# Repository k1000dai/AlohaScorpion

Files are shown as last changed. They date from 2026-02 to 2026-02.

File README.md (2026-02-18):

# AlohaScorpion

<p align="center">
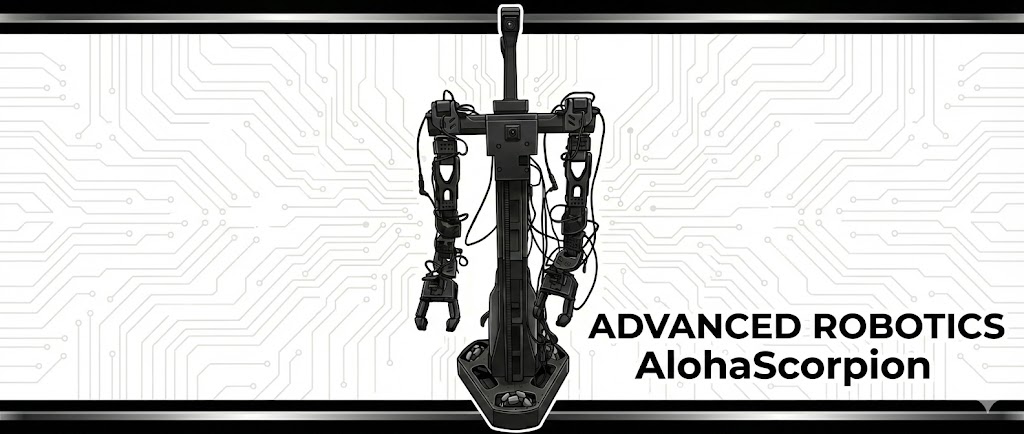
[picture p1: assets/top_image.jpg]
AlohaScorpion_top
  
</p>

AlohaScorpion is a 7 dof + gripper, dual-arm mobile manipulator with lift. It is designed for research and development in robotics, particularly in manipulation and mobile robotics.
This project is heavily inspired by the 

- Lerobot(https://github.com/k1000dai/lerobot)
- Alohamini(https://github.com/liyiteng/AlohaMini)
- Xlerobot(https://github.com/Vector-Wangel/XLeRobot)
- DualScorpion(https://github.com/momoiorg-repository/dual_scorpion)
- PincOpen(https://github.com/pollen-robotics/PincOpen)

## Update Log 
2/14 : Updated to the version 2.0. Better BOM, better chassis design, better arm position, pincopen gripper.

## To Do

- [ ] Add more details to the assembly instructions.
- [ ] Support VLA training.
- [ ] Support URDF and simulators.

## Images
<p align="center">
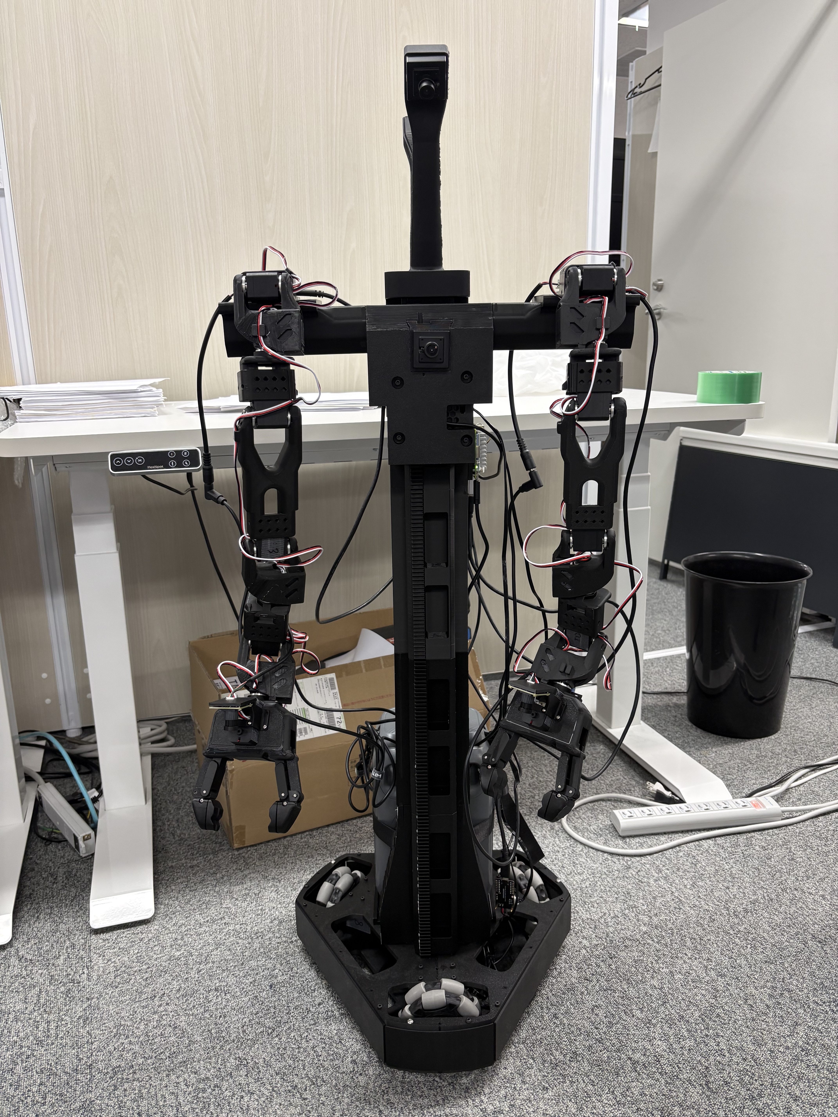
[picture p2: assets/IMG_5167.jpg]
AlohaScorpion
  
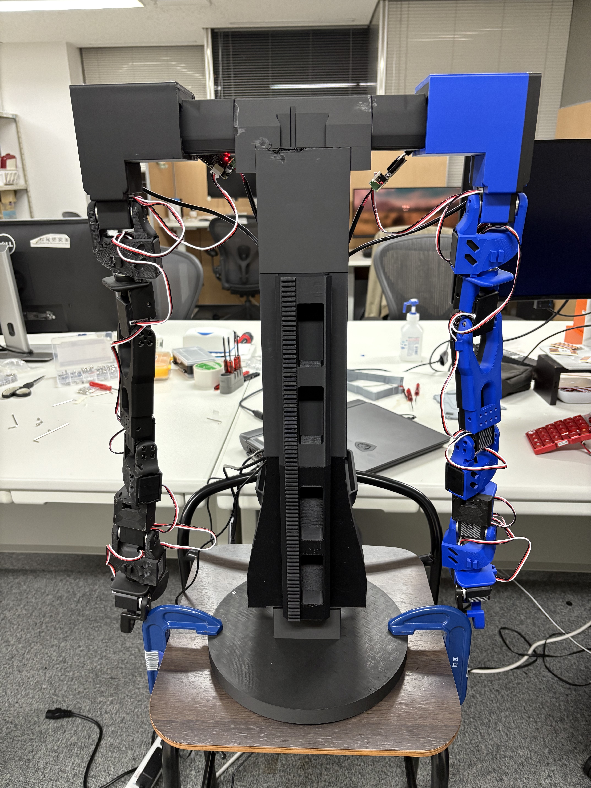
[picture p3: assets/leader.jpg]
leader
  
</p>

## Features
- 7 degrees of freedom per arm for enhanced manipulation capabilities. inspired by dual_scorpion

- Large battery capacity for extended operation time. based on the Xlerobot. Use Anker Solix C300 Portable Power Station 288Wh.

<p align="center">
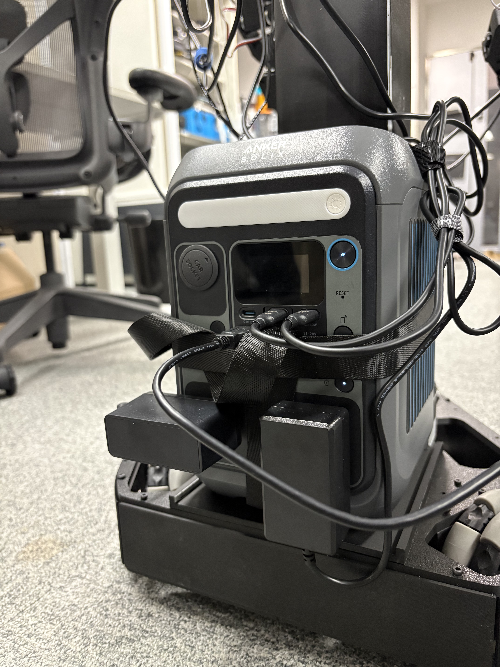
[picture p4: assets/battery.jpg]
battery
  
</p>

- Mobile base for navigation and mobility. based on alohamini. Using the Xlerobot chassis design, stronger and more stable than alohamini's chassis.

<p align="center">
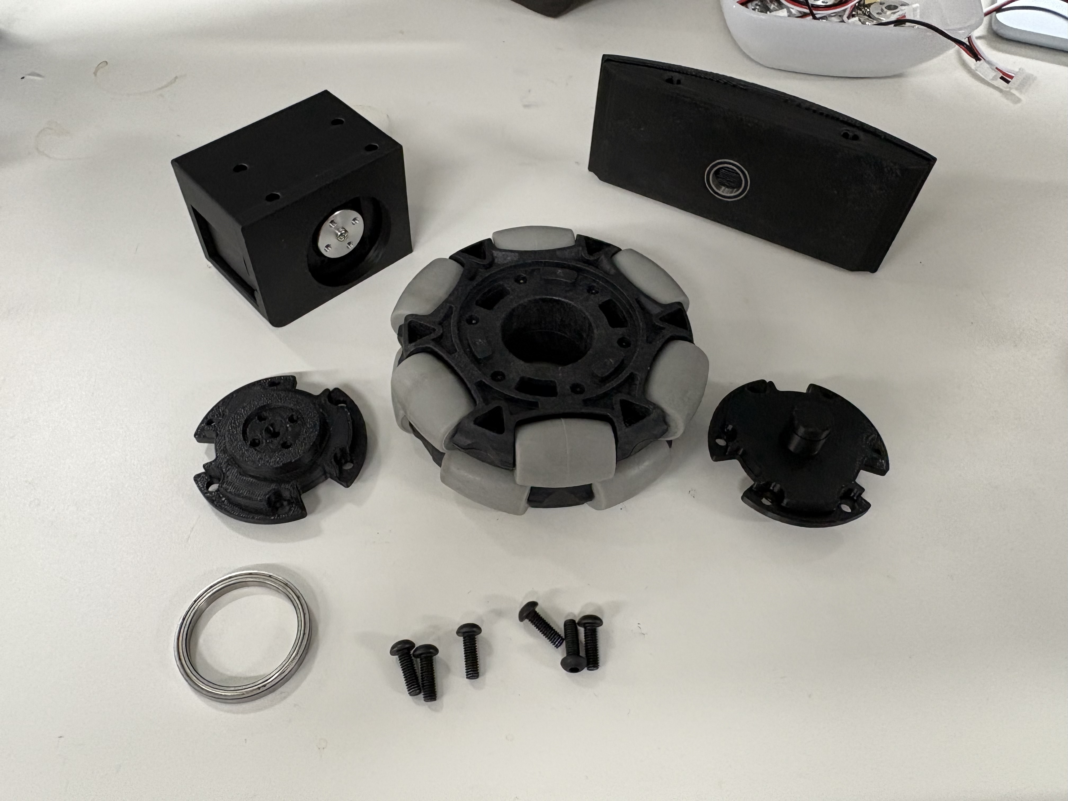
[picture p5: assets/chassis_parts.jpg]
chassis_parts
  
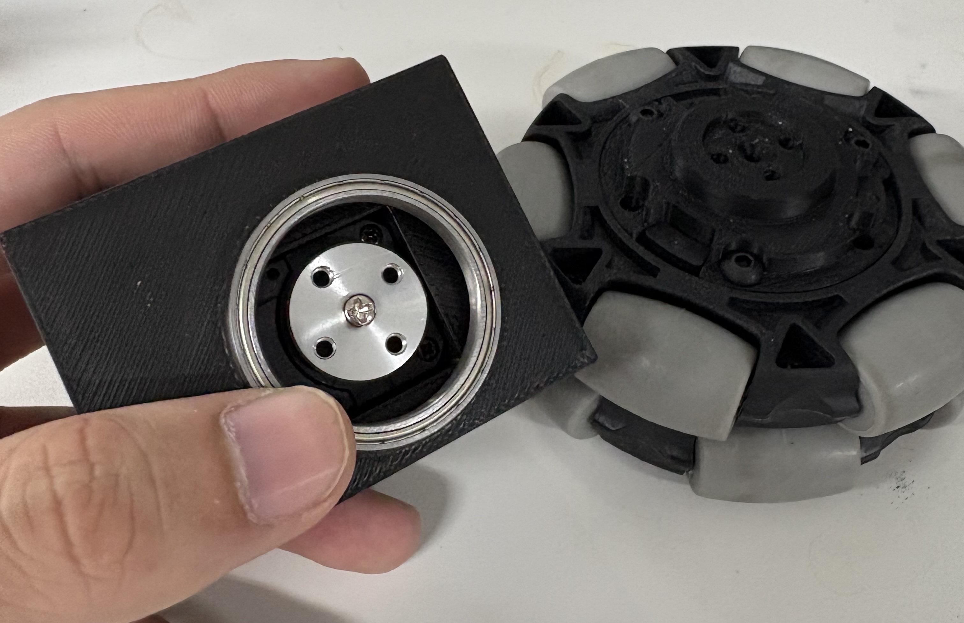
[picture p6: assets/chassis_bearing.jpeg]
chassis_bearing
  
</p>
<p align="center">
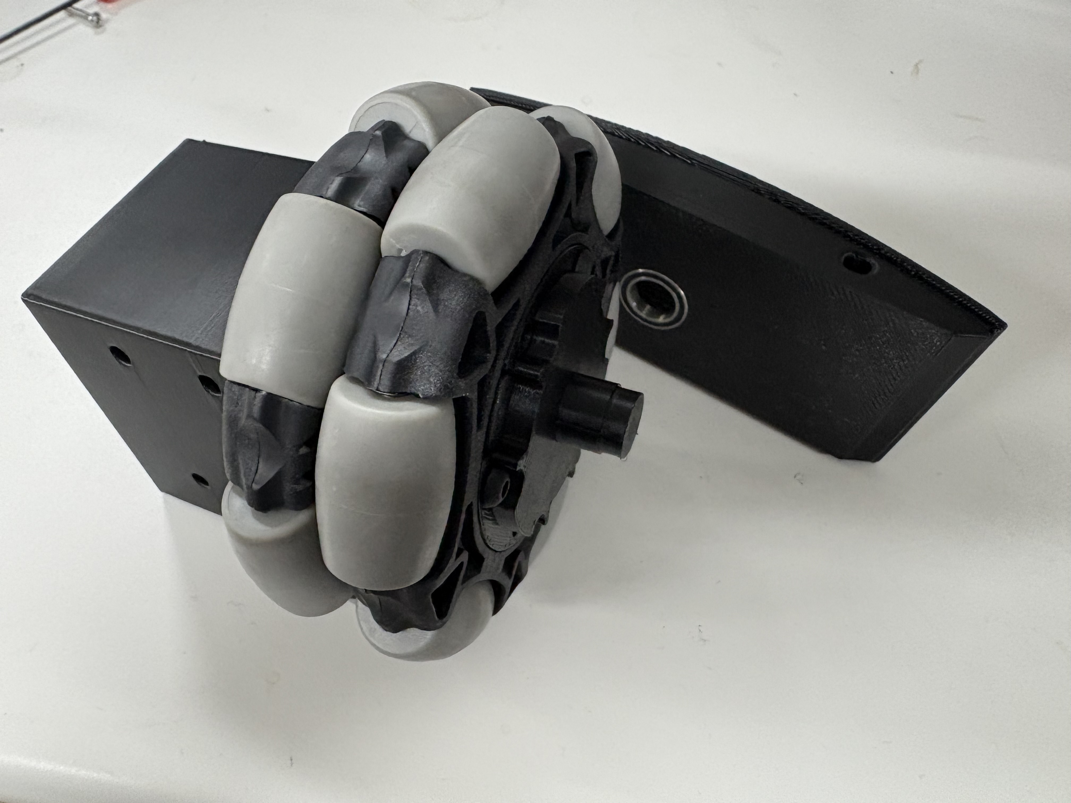
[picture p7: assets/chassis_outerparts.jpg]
chassis_outerparts
  
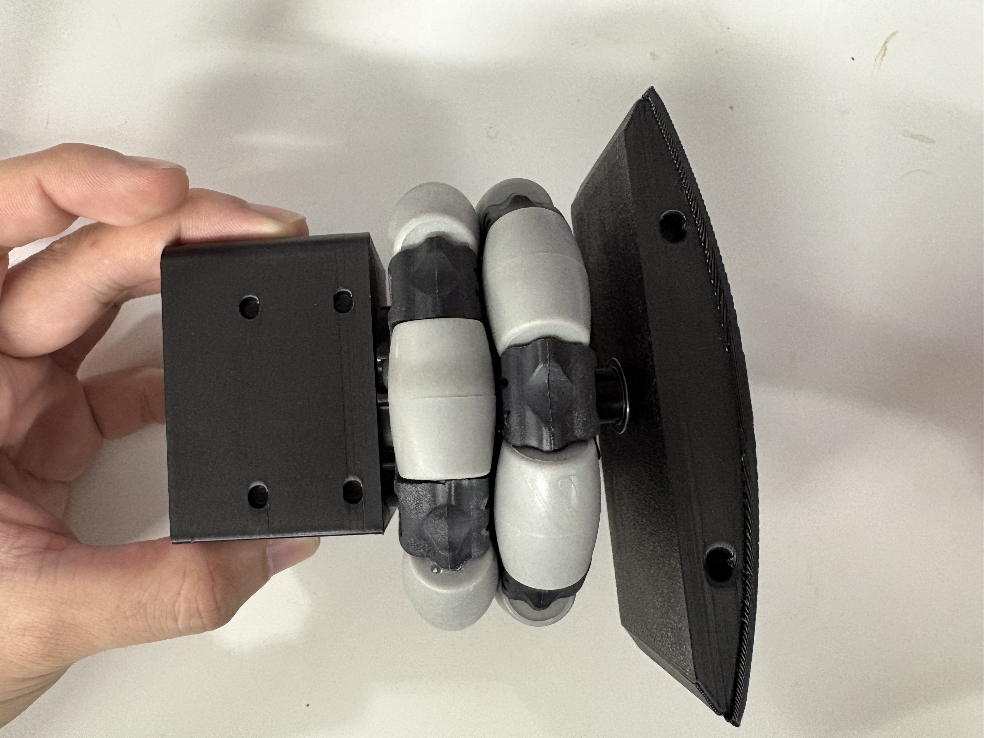
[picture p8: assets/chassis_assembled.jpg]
chassis_assembled
  
</p>

- Gripper for object handling. We use the PincOpen gripper, which is open-source parallel-finger gripper, derived from Pollen Robotics Reachy 2's gripper. It is compatible with the arms of AlohaScorpion.

<p align="center">
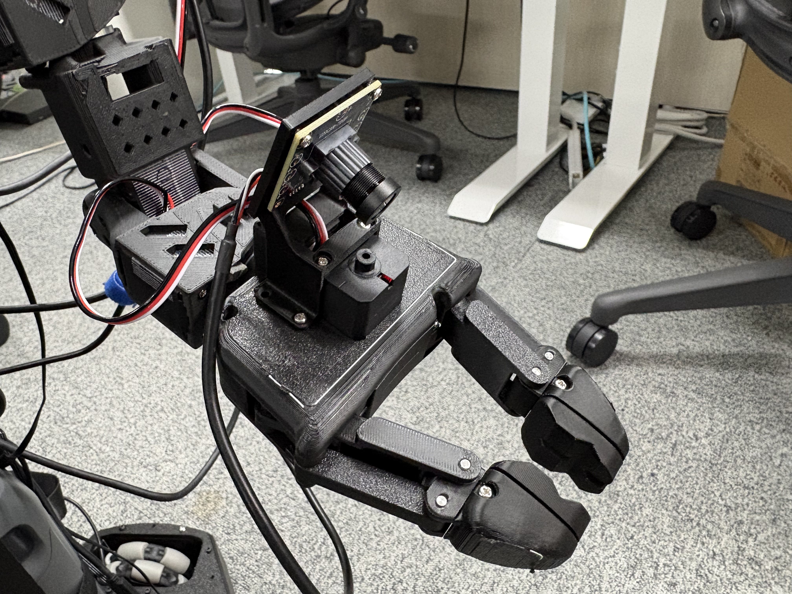
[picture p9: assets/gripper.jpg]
gripper
  
</p>

- Lift mechanism for vertical movement. based on Alohamini.

- Data collection and logging capabilities for research purposes. based on the lerobot framework. compatible with lerobot v0.4.3.

## Bill of Materials (BOM)
The complete Bill of Materials (BOM) can be found in the this Google Sheet : https://docs.google.com/spreadsheets/d/1W7IXB0Fid7SDyZUYEEcC63fRW-HXA5QO-rrAWQz4-Ek/edit?usp=sharing.

If you want to use  parallel-finger gripper, you can refer PincOpen github repository[https://github.com/pollen-robotics/PincOpen] for the BOM and assembly instructions. The gripper is compatible with the arms of AlohaScorpion. You need to use the updated mount plate in hardware/misc/stl/sointerface.stl.

## Assembly Instructions
Please see AlohaMini's assembly instructions as the mobile base and lift mechanism are almost the same.

Also, for the arms, please follow the dual_scorpion's assembly instructions. In order to keep the motor id, we use the 0 ~ 
7 motor for the arms. 8,9,10,11 motors are used for the mobile base and lift mechanism.

## Software

### Environment Setup
We setup the host with raspberry pi 5. You can also use any PC or raspberry pi 5 as the host.

install uv
```
curl -LsSf https://astral.sh/uv/install.sh | sh
```

```
git clone https://github.com/k1000dai/AlohaScorpion.git
cd AlohaScorpion
uv sync  --extra feetech
uv pip install zmq
```

### Running the Software
#### teleoperation
host side
```
python -m lerobot.robots.alohamini_scorpion.lekiwi_host
```

client side
```
python examples/alohamini_scorpion/teleoperate_bi.py \
--remote_ip ip_address_of_host \
```

#### data collection

- sample dataset : https://huggingface.co/datasets/k1000dai/alohascorpion_pick_plate_put_box
host side
```
python -m lerobot.robots.alohamini_scorpion.lekiwi_host
```
client side
```
python examples/alohamini_scorpion/record_bi.py \
--remote_ip ip_address_of_host \
--dataset user/my_dataset_name 
```

#### Replay
host side
```
python -m lerobot.robots.alohamini_scorpion.lekiwi_host
```

client side
```
python examples/alohamini_scorpion/replay_bi.py \
--remote_ip ip_address_of_host \
--dataset user/my_dataset_name
```

#### VLA training

ACT
```
lerobot-train \
  --dataset.repo_id=k1000dai/alohascorpion_pick_plate_put_box \
  --policy.type=act \
  --output_dir=outputs/train/alohascorpion_pick_plate_put_box\
  --job_name=alohascorpion_act \
  --policy.device=cuda \
  --wandb.enable=true \
  --policy.repo_id=k1000dai/alohascorpion_act
```

PI05
```
lerobot-train \↲
    --dataset.repo_id=k1000dai/alohascorpion_pick_plate_put_box \
    --policy.type=pi05 \
    --policy.pretrained_path=lerobot/pi05_base \
    --policy.compile_model=true \
    --policy.gradient_checkpointing=true \
    --output_dir=outputs/train/alohascorpion_pick_plate_put_box\
    --job_name=alohascorpion_pi05 \
    --policy.device=cuda \
    --policy.dtype=bfloat16 \
    --policy.freeze_vision_encoder=false \
    --policy.train_expert_only=false \
    --wandb.enable=true \
    --policy.repo_id=k1000dai/alohascorpion_pi05 \
    --batch_size=32
```

#### Evaluation model
```
python examples/alohamini_scorpion/evaluate_bi.py \
  --num_episodes 1 \
  --fps 10 \
  --episode_time 180  \
  --task_description "task_description"  \
  --hf_model_id k1000dai/act_alohascorpion  \
  --hf_dataset_id k1000dai/evaldataset   \
  --remote_ip ip_address_of_host
```
## License
This project is licensed under the Apache 2.0 License - see the [LICENSE](LICENSE) file for details.

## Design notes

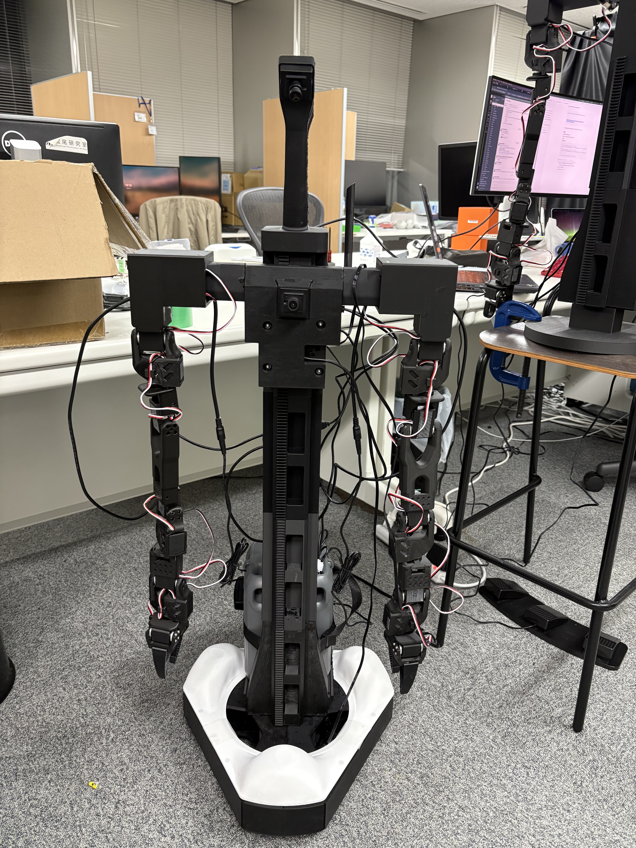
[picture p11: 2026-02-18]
assets/mainimage.jpg

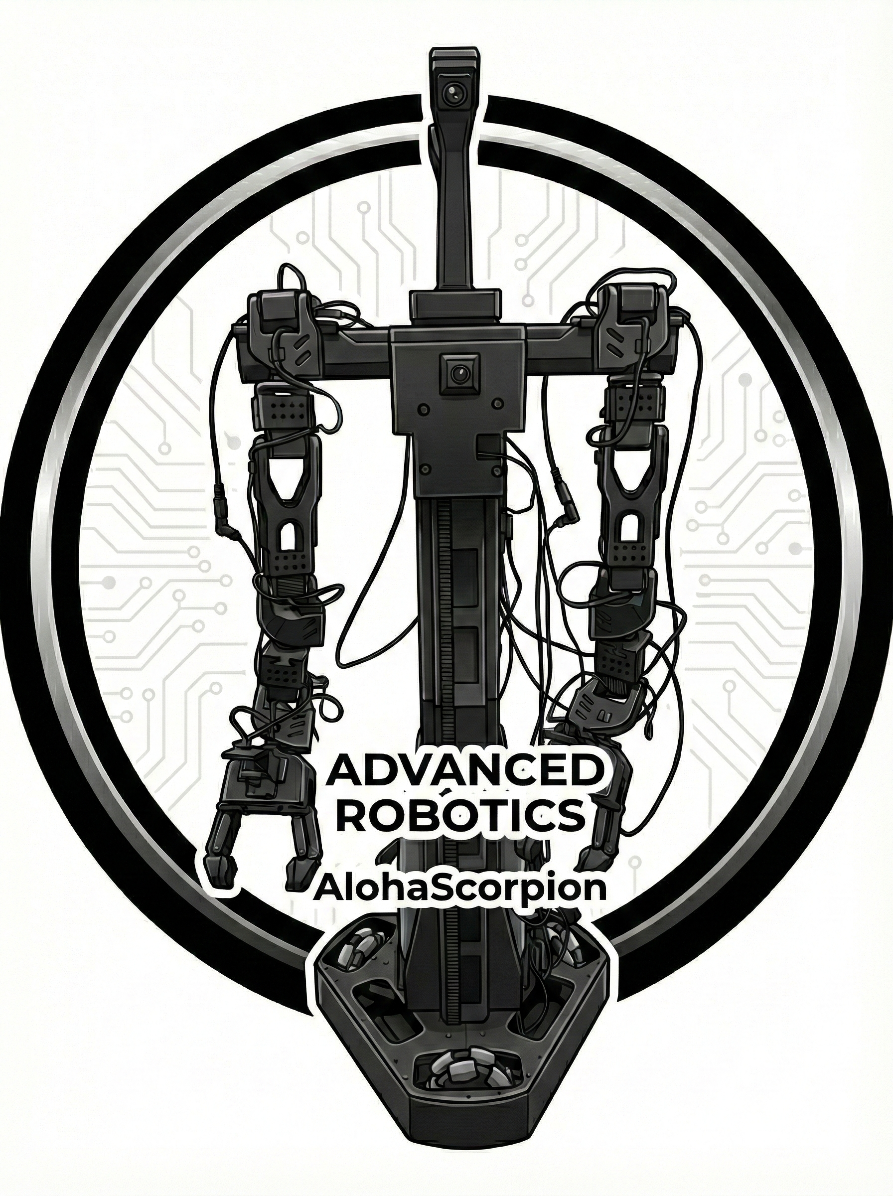
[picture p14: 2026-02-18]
assets/log.png

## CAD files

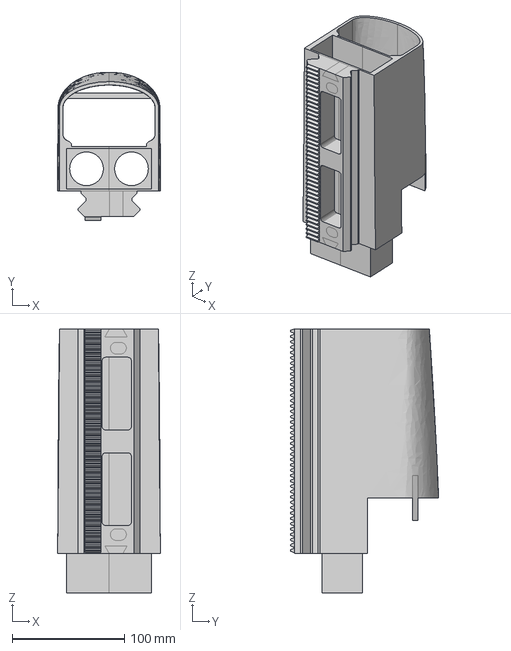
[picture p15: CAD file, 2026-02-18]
hardware/mobilebase/step/O_Main_Assembly_Post3.step
91.5 x 132.0 x 235.0 mm

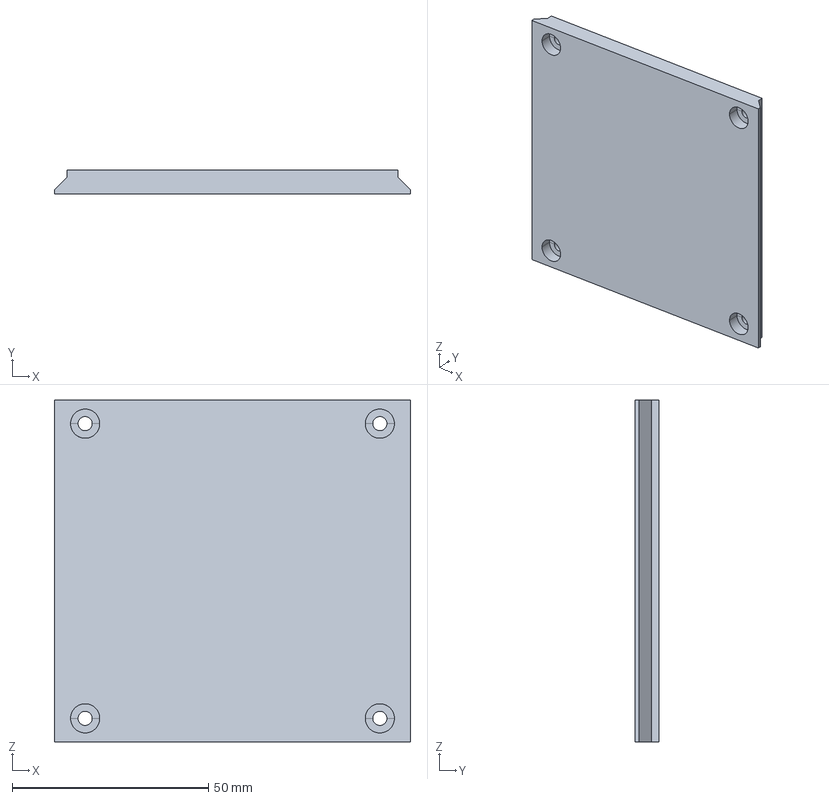
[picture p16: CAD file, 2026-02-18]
hardware/mobilebase/step/OB_Main_Monitor_Connector.stp
90.6 x 6.00 x 87.0 mm

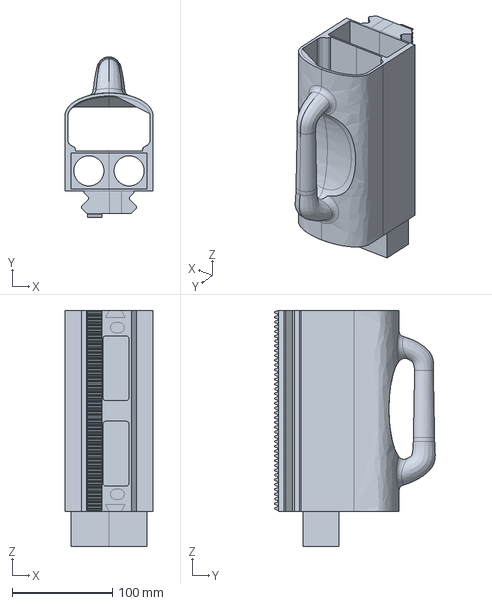
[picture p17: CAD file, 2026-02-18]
hardware/mobilebase/step/O_Main_Assembly_Post2.stp
88.1 x 159.9 x 235.0 mm

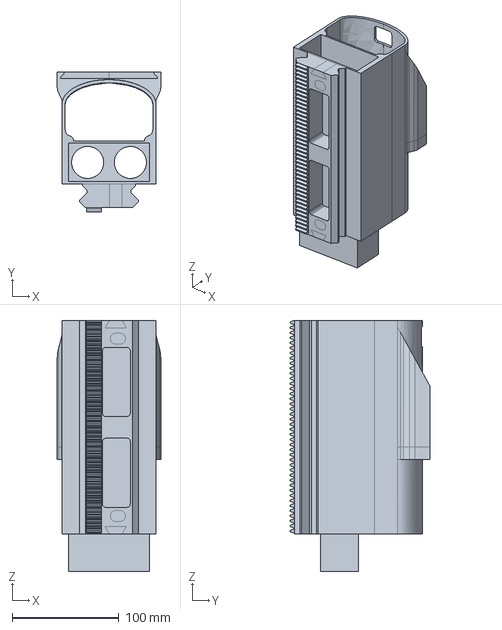
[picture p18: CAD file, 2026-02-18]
hardware/mobilebase/step/O_Main_Assembly_Post1.stp
97.0 x 130.7 x 235.0 mm

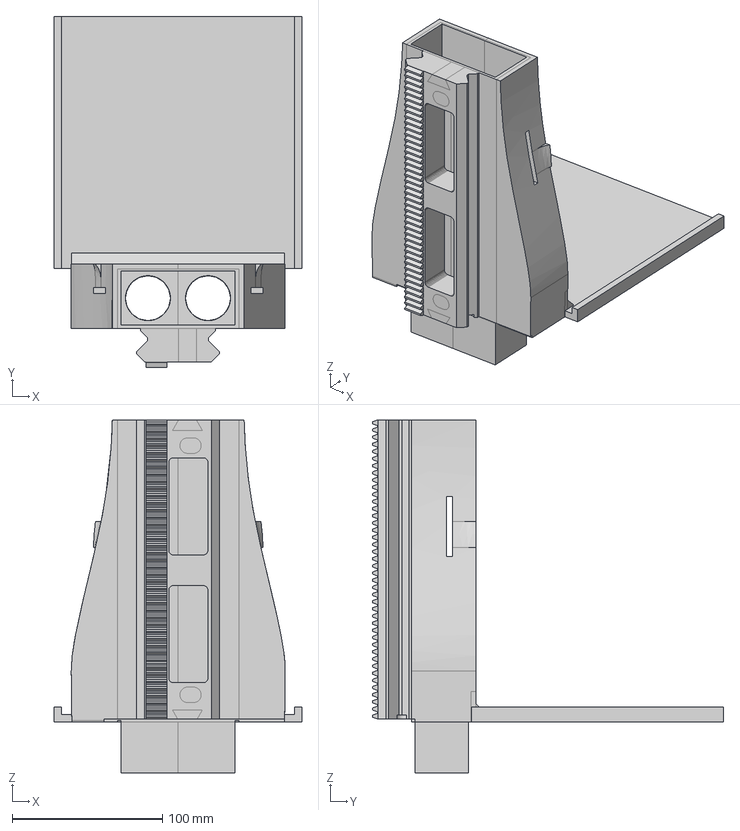
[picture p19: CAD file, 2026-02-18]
hardware/mobilebase/step/O_Main_Assembly_Post4_solaris.step
165.0 x 233.8 x 235.0 mm

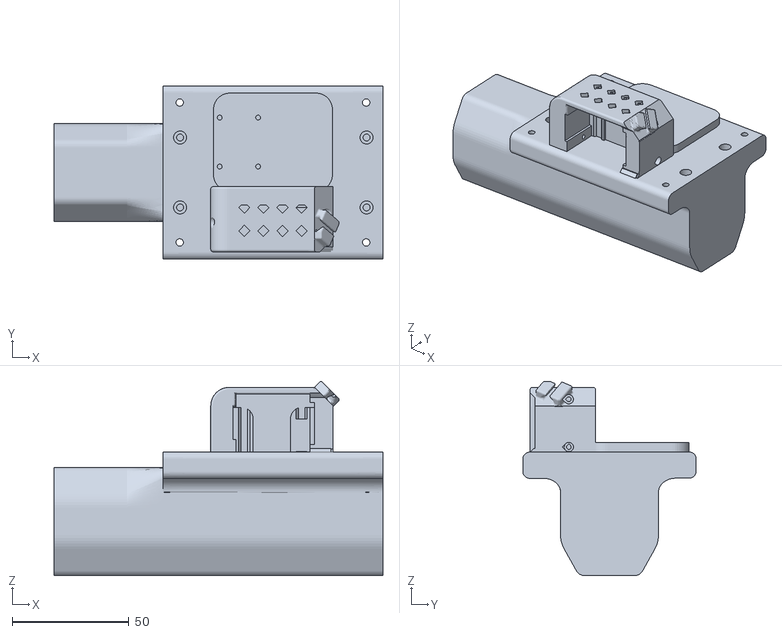
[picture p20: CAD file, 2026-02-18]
hardware/follower_arm/OB_T_Connector_Left_alohaminiver.stl
141.1 x 74.4 x 83.3

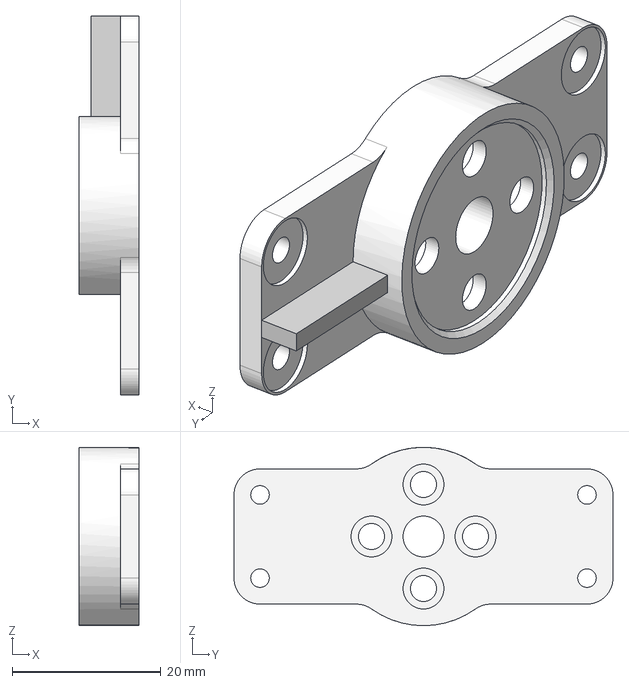
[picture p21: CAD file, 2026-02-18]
hardware/misc/step/sointerface.step
8.12 x 51.0 x 24.0 mm

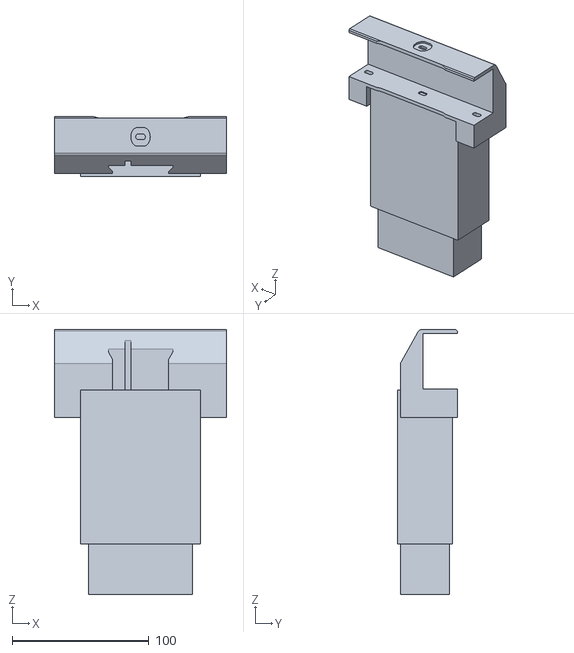
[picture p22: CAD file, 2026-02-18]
hardware/misc/stl/OB_T_Connector_Middle_leader.stl
126.0 x 43.6 x 194.0

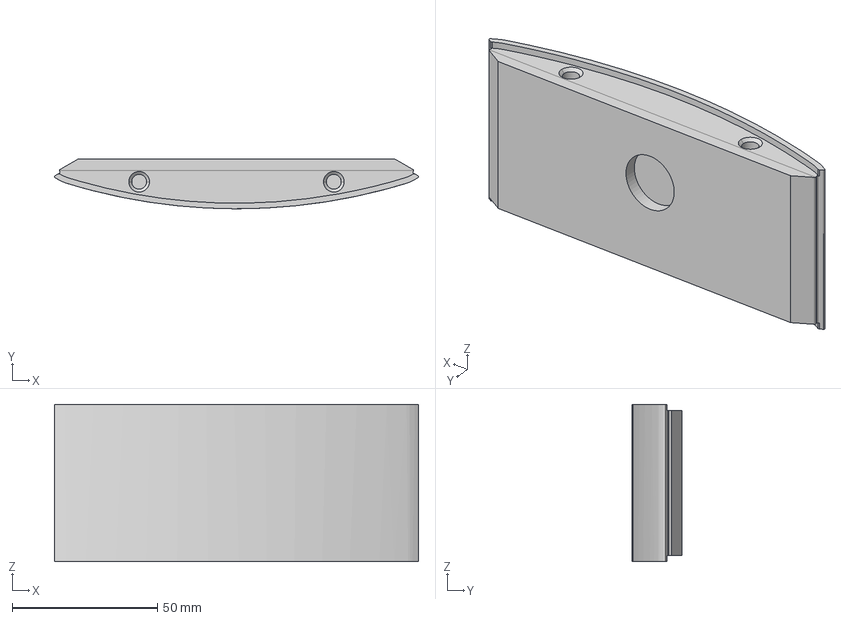
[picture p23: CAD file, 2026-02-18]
hardware/mobilebase/step/OB_Chassis_Bearing_Cover.step
125.5 x 17.1 x 54.2 mm

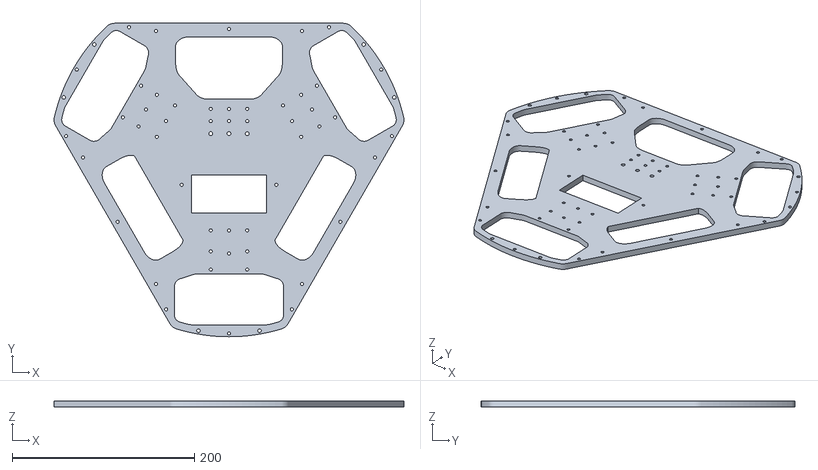
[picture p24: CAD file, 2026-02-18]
hardware/mobilebase/stl/O_Chassis_Lower_Plate_alohamini_40mmfront.step.stl
384.5 x 344.4 x 7.00

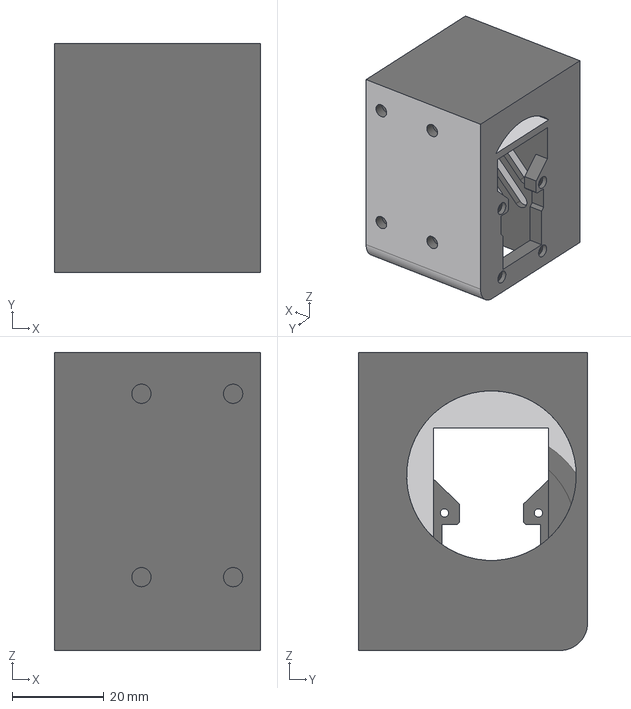
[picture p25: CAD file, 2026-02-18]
hardware/mobilebase/step/servo_mountv2.step
45.0 x 50.0 x 65.0 mm

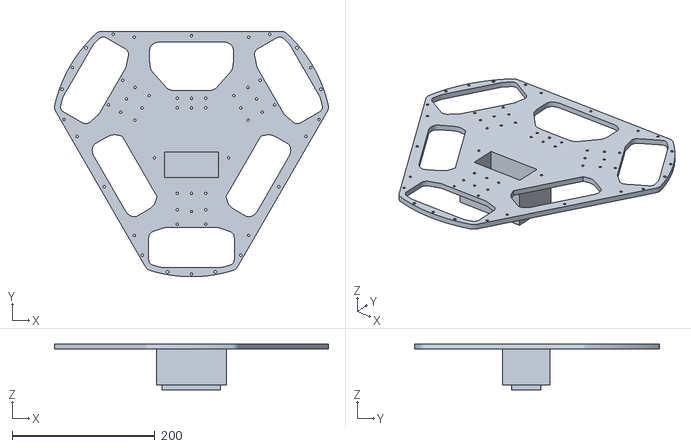
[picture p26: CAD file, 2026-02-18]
hardware/mobilebase/stl/O_Chassis_Upper_Plate_alohamini_40mmfront.step.stl
384.5 x 344.4 x 64.0

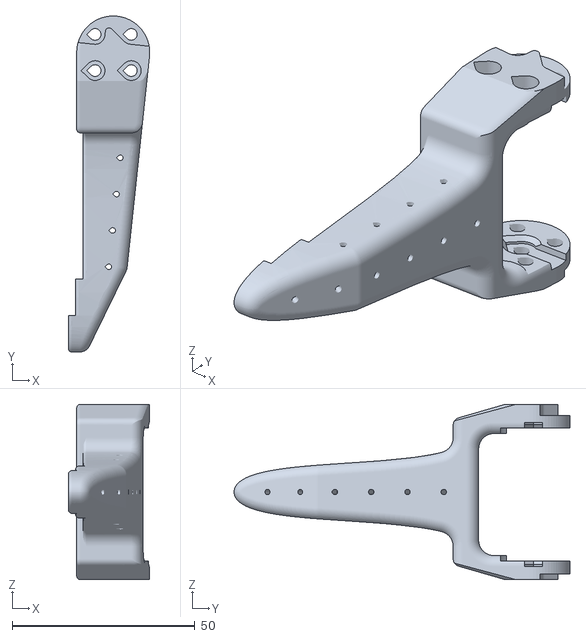
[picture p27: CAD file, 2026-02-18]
hardware/follower_arm/joint7_gripper_moving_jaw_R.stl
22.3 x 92.0 x 48.0

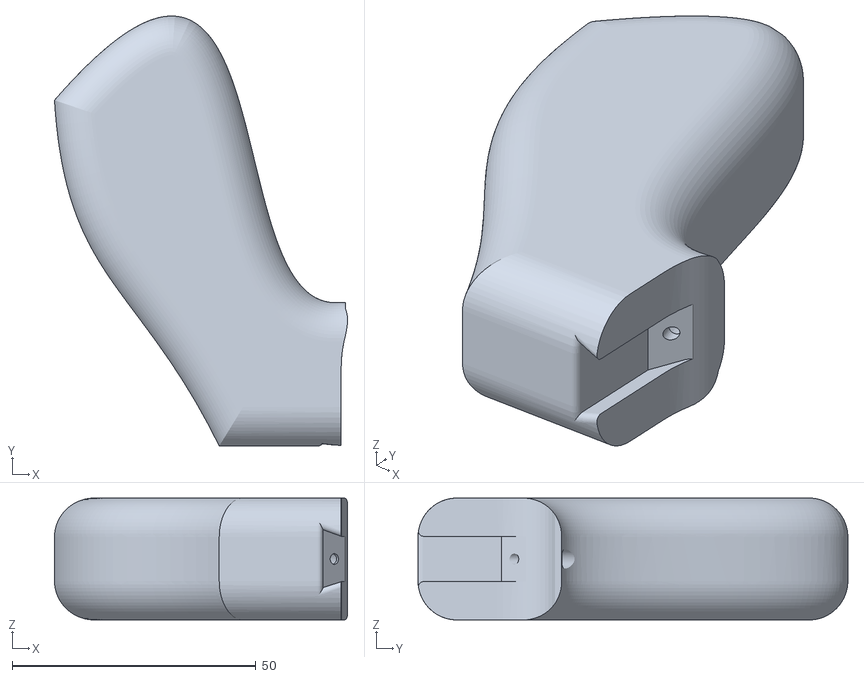
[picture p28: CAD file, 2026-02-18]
hardware/leader_arm/jpint7_gripper_hand_R.stl
60.1 x 88.1 x 25.0

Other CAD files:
hardware/leader_arm/OB_T_Connector_Right_alohaminiver.stl
hardware/follower_arm/OB_T_Connector_Right_alohaminiver.stl
hardware/misc/step/OB_T_Connector_Middle.step
hardware/follower_arm/joint1_wrist_roll_pitch_R.stl
hardware/follower_arm/joint1_wrist_roll_pitch_reverse_L.stl
hardware/follower_arm/joint2_new_dof_R.stl
hardware/follower_arm/joint2_new_dof_reverse_L.stl
hardware/follower_arm/joint3_under_arm_L.stl
hardware/follower_arm/joint3_under_arm_R.stl
hardware/follower_arm/joint4_wrist_roll_pitch_L.stl
hardware/follower_arm/joint4_wrist_roll_pitch_reverse_R.stl
hardware/follower_arm/joint5_new_dof_reverse_L.stl
hardware/follower_arm/joint5_new_dof_reverse_R.stl
hardware/follower_arm/joint6_wrist_roll_pitch_R.stl
hardware/follower_arm/joint6_wrist_roll_pitch_reverse_L.stl
hardware/follower_arm/joint7_wrist_roll_follower_L.stl
hardware/follower_arm/joint7_wrist_roll_follower_R.stl
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

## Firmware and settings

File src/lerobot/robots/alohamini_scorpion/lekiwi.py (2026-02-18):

#!/usr/bin/env python

# Copyright 2024 The HuggingFace Inc. team. All rights reserved.
#
# Licensed under the Apache License, Version 2.0 (the "License");
# you may not use this file except in compliance with the License.
# You may obtain a copy of the License at
#
#     http://www.apache.org/licenses/LICENSE-2.0
#
# Unless required by applicable law or agreed to in writing, software
# distributed under the License is distributed on an "AS IS" BASIS,
# WITHOUT WARRANTIES OR CONDITIONS OF ANY KIND, either express or implied.
# See the License for the specific language governing permissions and
# limitations under the License.

import inspect
import logging
import os
import time
from functools import cached_property
from typing import Any
import sys

import numpy as np

from lerobot.cameras.utils import make_cameras_from_configs
from lerobot.utils.errors import DeviceAlreadyConnectedError, DeviceNotConnectedError
from lerobot.motors import Motor, MotorCalibration, MotorNormMode
from lerobot.motors.feetech import (
    FeetechMotorsBus,
    OperatingMode,
)

from ..robot import Robot
from ..utils import ensure_safe_goal_position
from .config_lekiwi import LeKiwiConfig

logger = logging.getLogger(__name__)

from .lift_axis import LiftAxis, LiftAxisConfig


class LeKiwi(Robot):
    """
    The robot includes a three omniwheel mobile base and a remote follower arm.
    The leader arm is connected locally (on the laptop) and its joint positions are recorded and then
    forwarded to the remote follower arm (after applying a safety clamp).
    In parallel, keyboard teleoperation is used to generate raw velocity commands for the wheels.
    """

    config_class = LeKiwiConfig
    name = "lekiwi"

    def __init__(self, config: LeKiwiConfig):
        super().__init__(config)
        self.config = config
        norm_mode_body = MotorNormMode.DEGREES if config.use_degrees else MotorNormMode.RANGE_M100_100

        self.left_bus = FeetechMotorsBus(
            port=self.config.left_port,
            motors={
                # arm
                "arm_left_joint0": Motor(0, "sts3215", norm_mode_body),
                "arm_left_joint1": Motor(1, "sts3215", norm_mode_body),
                "arm_left_joint2": Motor(2, "sts3215", norm_mode_body),
                "arm_left_joint3": Motor(3, "sts3215", norm_mode_body),
                "arm_left_joint4": Motor(4, "sts3215", norm_mode_body),
                "arm_left_joint5": Motor(5, "sts3215", norm_mode_body),
                "arm_left_joint6": Motor(6, "sts3215", norm_mode_body),
                "arm_left_gripper": Motor(7, "sts3215", MotorNormMode.RANGE_0_100),
            },
            calibration=self.calibration,
        )

        self.right_bus = FeetechMotorsBus(
            port=self.config.right_port,
            motors={
                # arm
                "arm_right_joint0": Motor(0, "sts3215", norm_mode_body),
                "arm_right_joint1": Motor(1, "sts3215", norm_mode_body),
                "arm_right_joint2": Motor(2, "sts3215", norm_mode_body),
                "arm_right_joint3": Motor(3, "sts3215", norm_mode_body),
                "arm_right_joint4": Motor(4, "sts3215", norm_mode_body),
                "arm_right_joint5": Motor(5, "sts3215", norm_mode_body),
                "arm_right_joint6": Motor(6, "sts3215", norm_mode_body),
                "arm_right_gripper": Motor(7, "sts3215", MotorNormMode.RANGE_0_100),
            },
            calibration=self.calibration,
        )

        self.base_bus = FeetechMotorsBus(
            port=self.config.base_port,
            motors={
                # base
                "base_left_wheel": Motor(8, "sts3215", MotorNormMode.RANGE_M100_100),
                "base_back_wheel": Motor(9, "sts3215", MotorNormMode.RANGE_M100_100),
                "base_right_wheel": Motor(10, "sts3215", MotorNormMode.RANGE_M100_100),
                "lift_axis": Motor(11, "sts3215", MotorNormMode.DEGREES),
            },
            calibration=None,
        )

        self.left_arm_motors = [m for m in self.left_bus.motors if m.startswith("arm_left_")]
        self.base_motors = [m for m in self.base_bus.motors if m.startswith("base_")]
        # self.left_arm_motors  = [m for m in self.left_bus.motors        if m.startswith("right_arm_")]

        self.right_arm_motors = [
            m for m in (self.right_bus.motors if self.right_bus else []) if m.startswith("arm_right_")
        ]

        # self.arm_motors = [motor for motor in self.left_bus.motors if motor.startswith("arm")]
        # self.base_motors = [motor for motor in self.left_bus.motors if motor.startswith("base")]

        self.cameras = make_cameras_from_configs(config.cameras)

        self.lift = LiftAxis(
            LiftAxisConfig(bus="base"),
            bus_left=self.left_bus,
            bus_right=self.right_bus,
            bus_base=self.base_bus,
        )

    @property
    def _state_ft(self) -> dict[str, type]:
        return dict.fromkeys(
            (
                "arm_left_joint0.pos",
                "arm_left_joint1.pos",
                "arm_left_joint2.pos",
                "arm_left_joint3.pos",
                "arm_left_joint4.pos",
                "arm_left_joint5.pos",
                "arm_left_joint6.pos",
                "arm_left_gripper.pos",
                "arm_right_joint0.pos",
                "arm_right_joint1.pos",
                "arm_right_joint2.pos",
                "arm_right_joint3.pos",
                "arm_right_joint4.pos",
                "arm_right_joint5.pos",
                "arm_right_joint6.pos",
                "arm_right_gripper.pos",
                "x.vel",
                "y.vel",
                "theta.vel",
                "lift_axis.height_mm",  # ← 新增
                # "lift_axis.vel",         # ← 新增（可选，做调试用）
            ),
            float,
        )

    @property
    def _cameras_ft(self) -> dict[str, tuple]:
        return {
            cam: (self.config.cameras[cam].height, self.config.cameras[cam].width, 3) for cam in self.cameras
        }

    @cached_property
    def observation_features(self) -> dict[str, type | tuple]:
        return {**self._state_ft, **self._cameras_ft}

    @cached_property
    def action_features(self) -> dict[str, type]:
        return self._state_ft

    # @property
    # def is_connected(self) -> bool:
    #     return self.left_bus.is_connected and all(cam.is_connected for cam in self.cameras.values())

    @property
    def is_connected(self) -> bool:
        cams_ok = all(cam.is_connected for cam in self.cameras.values())
        return (
            self.left_bus.is_connected
            and (self.right_bus.is_connected if self.right_bus else True)
            and (self.base_bus.is_connected if self.base_bus else True)
            and cams_ok
        )
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

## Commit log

2026-02-18 update BOM
    [OB_Chassis_Bearing_Cover.stl, OB_Chassis_Bearing_Cover.stp, OB_Chassis_Servo_Mount.stl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]
2026-02-18 Dev/2wheel pincopen (#1)
    [OB_Chassis_Bearing_Cover.step, OB_Chassis_Bearing_Cover.stl, OB_Chassis_Bearing_Cover.stp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]
